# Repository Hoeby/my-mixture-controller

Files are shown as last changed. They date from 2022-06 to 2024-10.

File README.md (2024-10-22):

# mixture-controller
RC engine mixture controller.

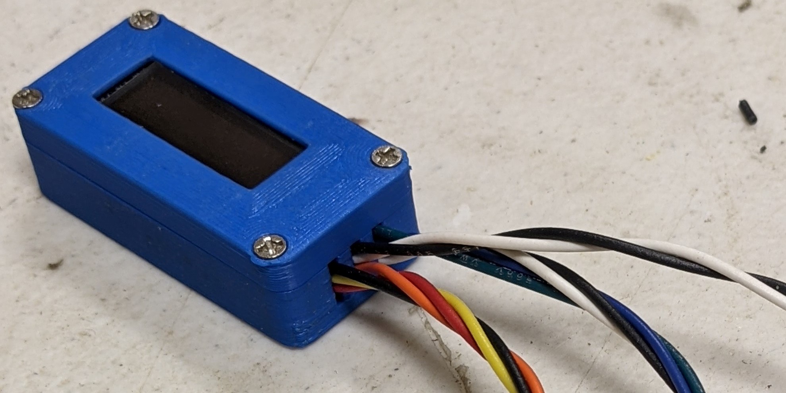
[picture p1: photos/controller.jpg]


This controller works with a stihl solenoid part number 0000 120 5111 and a custom solenoid housing (https://github.com/raleighcopter/my-mixture-controller/blob/main/photos/solenoid%20housing.pdf) to modulate gasoline flow to a conventional methanol carburator. This allows us to generate a custom fuel mixture curve on our transmitter that is slaved to the throttle channel output. The result is that we can vary the fuel:air mixture across the entire throttle range to make the engine run near stoichiometric fuel:air ratio at idle, full throttle, and every point in between. Without the solenoid and controller, our methanol engines run extremely rich in the middle. 

The controller takes an RC channel and maps a 1000 uS - 2000 uS channel pulse to a PWM solenoid pulse. Additionally, the controller measures atmospheric pressure and temperature and adjusts the fuel amount to maintain the ideal mixture regardless of the weather or altitude (which constantly changes as we fly our models). We have engines that were tuned at 85 degrees F that run just as well at 35 degrees F without touching the needles. 

I currently have my OS FT120-ii and Saito FA72 converted and Bert (the man behind the idea who designed the solenoid housing) has engines ranging from an asp 0.30 four stroke up to an ASP 1.6 boxer and a larger radial converted and running well. This conversion has been used on 2 stroke engines, 4 stroke engines, single  and twin cylinder engines and radial multi-cylinder engines.

I built the controller using a seeduino Xiao an IRLD110pbf MOSFET, a 2.2k resistor, a diode, a bmp280, and optionally, a 128x32 oled display and I've tested it on 4s NiMH and 2s LiFePo. Power comes in on the power and ground pads on the back of the Xiao. 

If you're powering your controller with a 2s LiFePo battery, wire a 1n4003 diode or something similar in the red wire before feeding power to the power pad or the Vcc pin. if you're powering your controller with a 4S NiMh, omit the diode and instead, wire a pololu s7v7f5 5 volt buck/boost converter inline.

The solenoid, bmp280, and optional display grab 3.3 volts from the Xiao's 3.3v pin. The MOSFET is wired to D3 and the RC channel is wired to D2. There's only 1 ground pad on the back and one ground pin so I doubled up on the pad on the back because I need 3 grounds.

I wired a 2.2k resistor across the MOSFET's gate and source (an 0805 smt resistor works really well here but a 1/8 watt resistor also works) and added a short piece of wire to those pins before I slipped some heat shrink over the separate pins. I soldered the wire that runs to the solenoid to the MOSFET's drain, trimmed the pins and then covered the entire MOSFET with heat shrink. After it was covered with heat shrink, I soldered the wire from the MOSFET's gate to D3 and the wire from the MOSFET's source to ground.

SDA and SCL from the bmp280 go to D4 and D5 and the optional display also uses these connections. if you measure resistance of about 10k between SDO and ground on the bmp280 it has a base address of 0x76. otherwise it has a base address of 0x77 and you need to change the base address at the top of the controller code. 

If you're building this with an oled display, wire the display to the same 4 points that the bmp280 is connected: 3.3v, ground, SDA, and SCL. You can wire it in parallel or in series with the bmp280.

if you're using this with an opentx transmitter and want s.port data, connect your s.port to pin 0 of the Xiao.

ebay/china is the least expensive source for bmp280 sensors at about $1 each and 128x32 oled displays at about $2.50. Be aware that we've seen fairly high failure rates on the China sourced bmp280 boards. As a result, the solenoid will signal a failed sensor at startup by buzzing for half a second and then remaining quiet for another half second and repeating indefinitely..

you'll need to install a few libraries in the arduino IDE: adafruit bmp280, adafruit ssd1306, adafruit GFX library and the frsky s.port sensor library by herman kruisman. you'll also need to add the seeeduino xiao board definition using the board manager.

build photos as well as parts lists and assembly instructions are on the wiki at https://github.com/raleighcopter/my-mixture-controller/wiki

for support, post in the thread at https://www.rcuniverse.com/forum/engine-conversions-92/11699946-electronic-solutions-modifying-glow-engines-all-sizes-gasoline.html

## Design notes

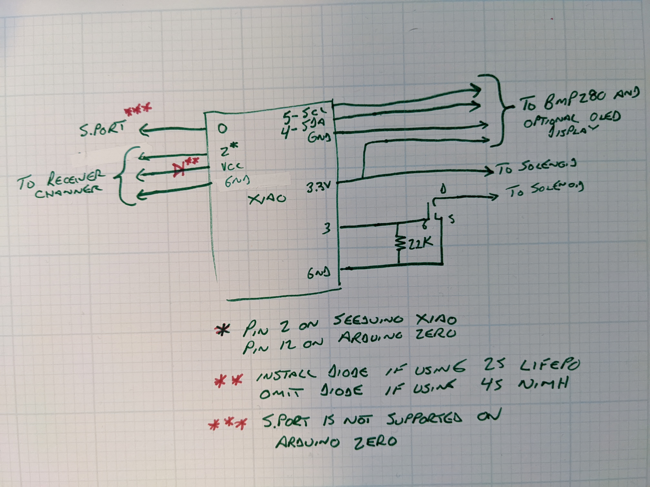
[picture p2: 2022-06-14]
photos/xiao schematic.jpg

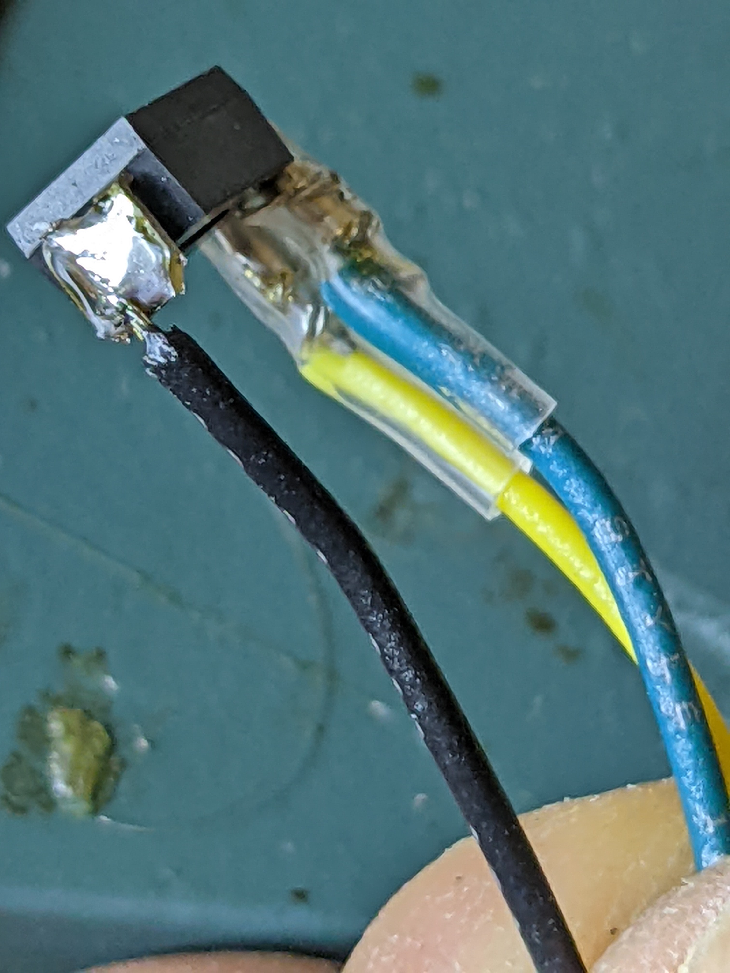
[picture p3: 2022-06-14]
photos/zero_11.jpg

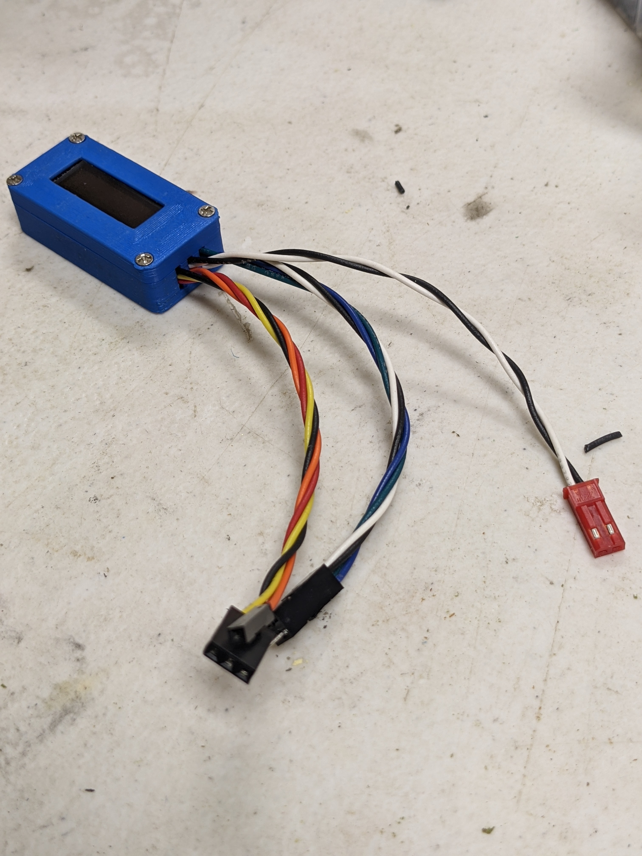
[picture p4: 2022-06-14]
photos/c1.jpg

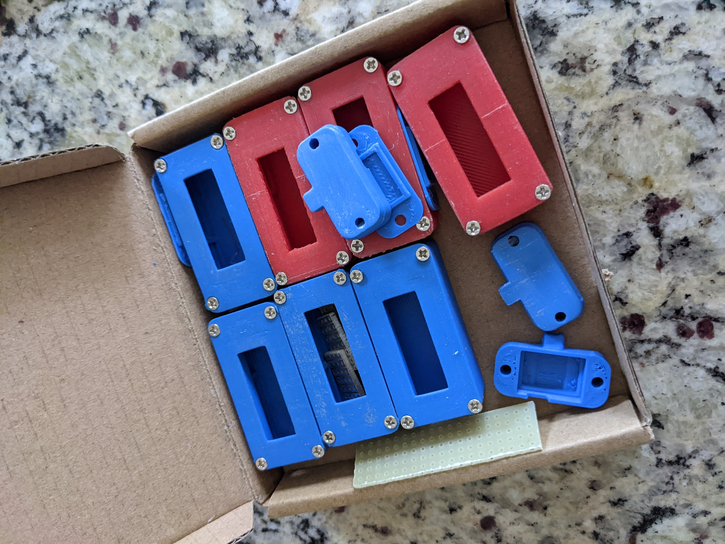
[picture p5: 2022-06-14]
photos/c2.jpg

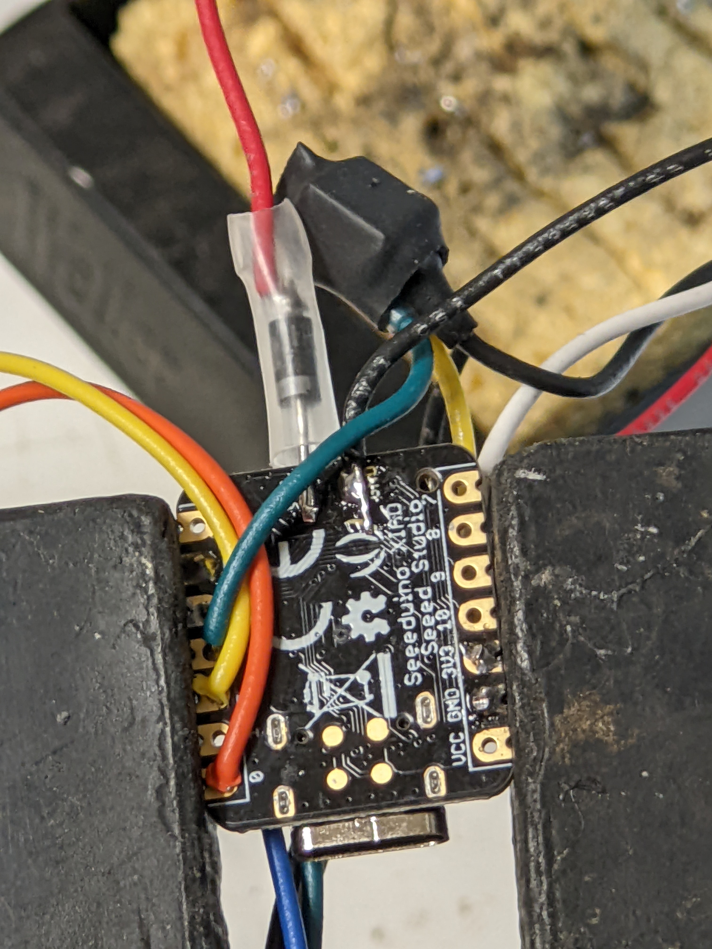
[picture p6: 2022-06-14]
photos/c12.jpg

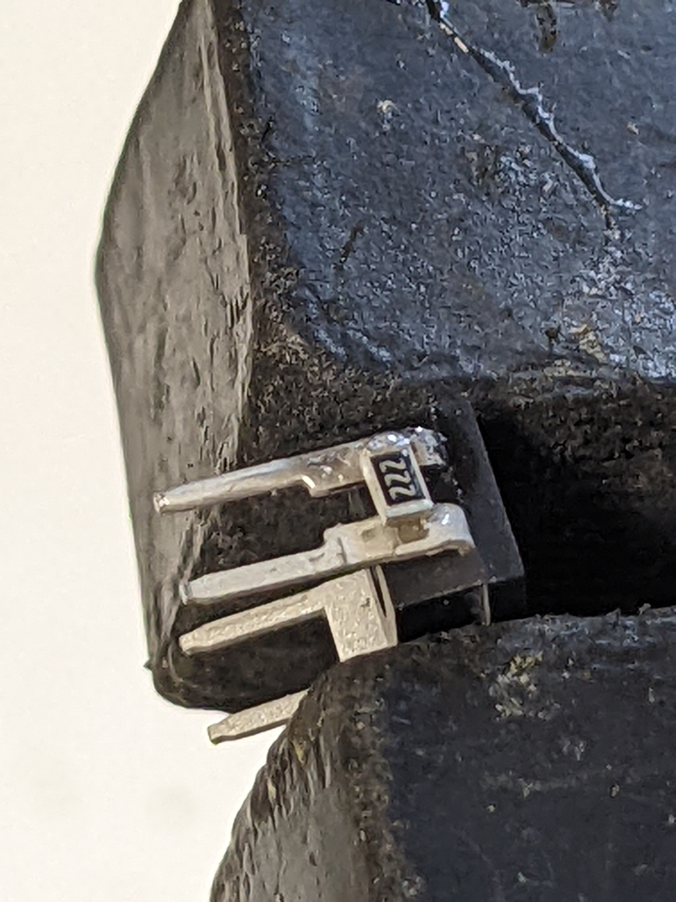
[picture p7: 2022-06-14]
photos/c4.jpg

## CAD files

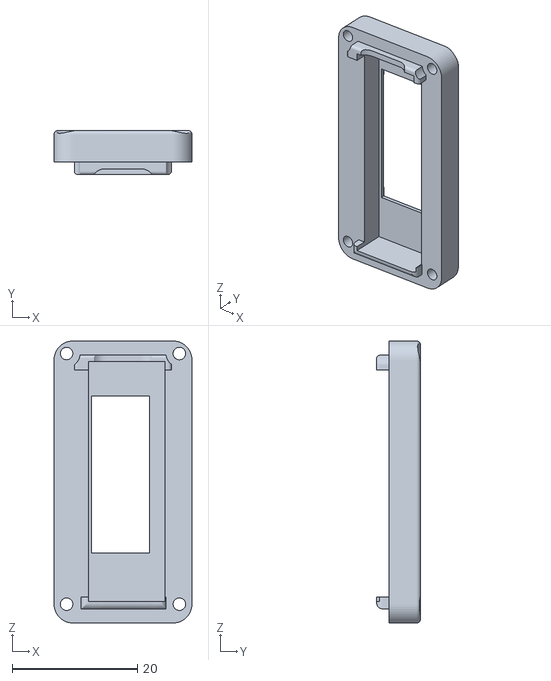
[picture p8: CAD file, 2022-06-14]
case_files/OLED lid.stl
22.0 x 7.00 x 45.0

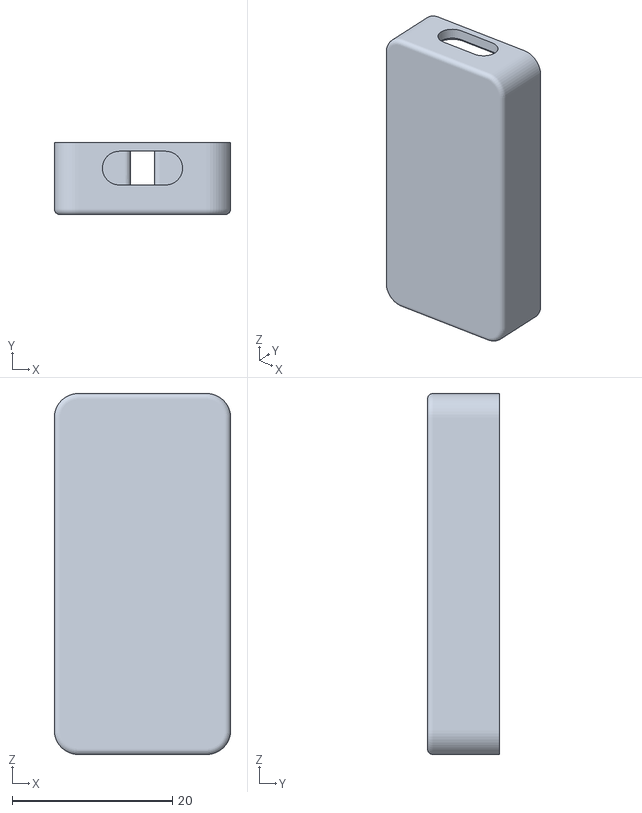
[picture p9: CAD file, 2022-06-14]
case_files/AMC case v9.stl
22.0 x 9.00 x 45.0

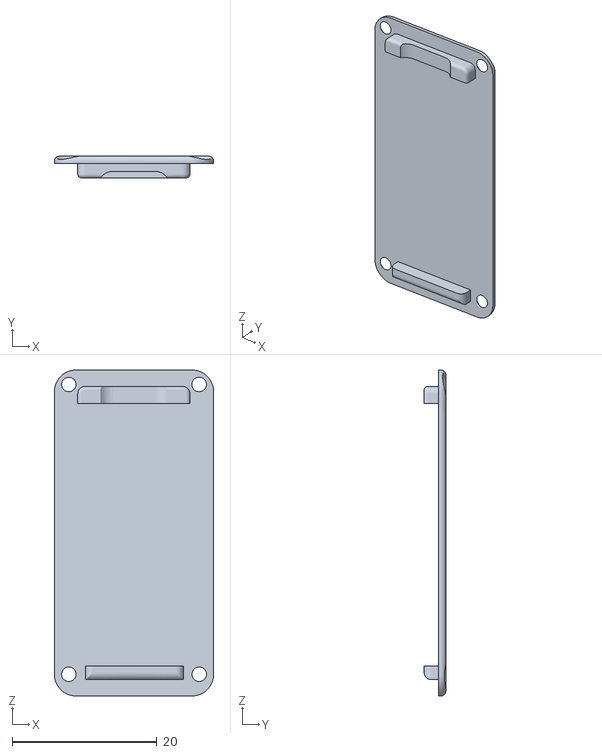
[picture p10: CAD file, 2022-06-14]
case_files/No OLED Lid.stl
22.0 x 3.00 x 45.0

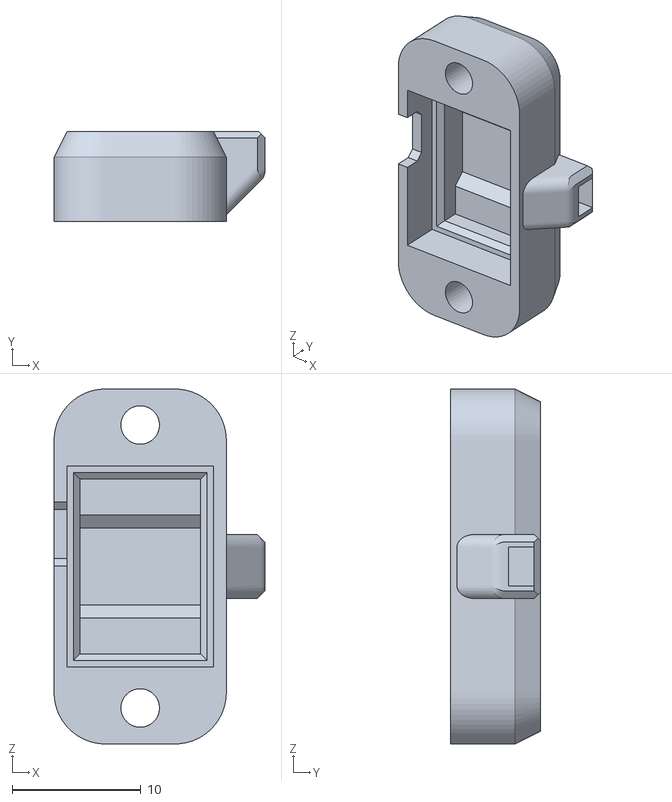
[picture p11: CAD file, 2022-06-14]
case_files/BMP280 Case.stl
16.4 x 7.00 x 27.6

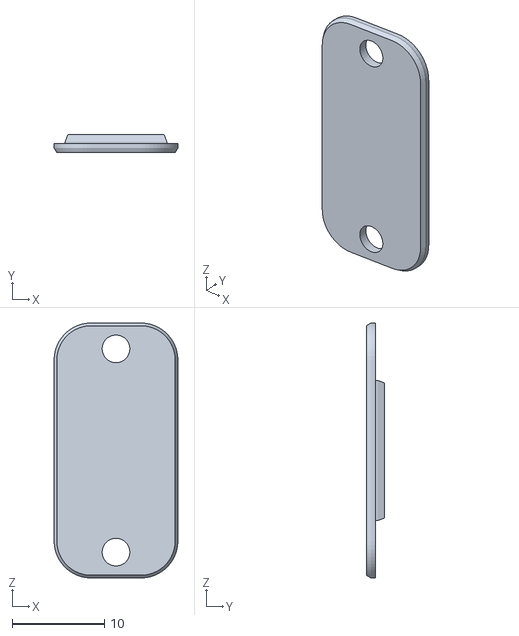
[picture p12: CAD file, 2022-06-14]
case_files/BMP280 cover.stl
13.4 x 2.00 x 27.6

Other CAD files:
brackets/asp ft1.6 bmp280 bracket v1.f3d
brackets/bmp280_bracket_OSft120.f3d
case_files/AMC case.f3d

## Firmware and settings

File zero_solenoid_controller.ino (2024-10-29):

//this code is written for the Arduino Zero by david taylor and released under the 
//GNU general public license V3.0. Permissions of this strong copyleft license are 
//conditioned on making available complete source code of licensed works and modifications,
//which include larger works using a licensed work, under the same license. Copyright and 
//license notices must be preserved. Contributors provide an express grant of patent rights.
// Also, Gary Cee from rcgroups is a douchebag 

//pin d3 controls the solenoid
//pin d12 is the rc channel input
//adjust reference temp (kelvin), pressure (paschal), and rc channel pin here
const int reference_temp = 283;
const int reference_pressure = 100000;

// Fallback temp and pressure replace actual measured values if the sensor fails during
// a flight. I estimate anything between this temp and 35 °F higher will cause the engine
// to run rich. Set fallback temp to the lowest temperature you're likely to fly in.
const int fallback_temp = 0;
const int fallback_pressure = 102000;
const int rc_functionPin = 12;

//OLED addresses are 0x3C or 0x3D
#define OLED_ADDR   0x3C

//BMP280 addresses are 0x76 or 0x77
#define BMP280_ADDR   0x76

//****************************************************************************************
// **********************  DO NOT EDIT ANYTHING BELOW THIS LINE  *************************
//****************************************************************************************

unsigned long old_time;
int update_display;
const long display_interval = 1000; 
volatile unsigned long pulse_start_time = 0L;
volatile unsigned long pulse_now = 0L;
volatile unsigned long channel_pulse = 0L;
volatile unsigned long pulse_old = 0L;
volatile unsigned long adjusted_pulse = 0L;
volatile unsigned long solenoid_pulse = 0L;
volatile unsigned long usable_pulse = 0L;
int channel;
int bmp_error = 0;
char _buffer[9];

#include <Wire.h>
#include <Adafruit_GFX.h>      // include Adafruit graphics library
#include <Adafruit_SSD1306.h>  // include Adafruit SSD1306 OLED display driver
#include <Adafruit_BMP280.h>   // include Adafruit BMP280 sensor library

Adafruit_BMP280 bmp; // I2C
Adafruit_SSD1306 display(-1);  // initialize Adafruit display library, share reset with xiao reset

void setup() {
  
// initialize the SSD1306 OLED display with I2C address = 0x3C
  display.begin(SSD1306_SWITCHCAPVCC, OLED_ADDR);
// clear the display buffer.
  display.clearDisplay();
  display.setTextSize(1);   // text size = 1
  display.setTextColor(WHITE, BLACK);  // set text color to white and black background

//uncomment the next line to debug  
//SerialUSB.begin(115200);

  pinMode(rc_functionPin, INPUT);
  attachInterrupt(rc_functionPin, RCpinread, CHANGE);

  if (!bmp.begin(BMP280_ADDR, BMP280_CHIPID)) {
//  SerialUSB.println(F("Could not find a valid BMP280 sensor, check wiring or try a different address!"));
    bmp_error = 1;
  }
  
  bmp.setSampling(Adafruit_BMP280::MODE_NORMAL,     /* Operating Mode. */
                  Adafruit_BMP280::SAMPLING_X2,     /* Temp. oversampling */
                  Adafruit_BMP280::SAMPLING_X16,    /* Pressure oversampling */
                  Adafruit_BMP280::FILTER_X16,      /* Filtering. */
                  Adafruit_BMP280::STANDBY_MS_500); /* Standby time. */

//check for bad data from bmp280 and set error flag
  if (bmp.readTemperature() >= 85) bmp_error = 1;
  if (bmp.readPressure() >= 110000) bmp_error = 1;                  

//setup timer regisiters
  pinMode(3, OUTPUT);
  REG_GCLK_GENDIV = GCLK_GENDIV_DIV(232) |       // Divide the main clock down by some factor to get generic clock
                    GCLK_GENDIV_ID(4);            // Select Generic Clock (GCLK) 4
  while (GCLK->STATUS.bit.SYNCBUSY);              // Wait for synchronization

  REG_GCLK_GENCTRL = GCLK_GENCTRL_IDC |           
                     GCLK_GENCTRL_GENEN |         // Enable GCLK4
                     GCLK_GENCTRL_SRC_DFLL48M |   // Set the 48MHz clock source
                     GCLK_GENCTRL_ID(4);          // Select GCLK4
  while (GCLK->STATUS.bit.SYNCBUSY);              // Wait for synchronization

// Enable the port multiplexer for the digital pin. 
  PORT->Group[g_APinDescription[3].ulPort].PINCFG[g_APinDescription[3].ulPin].bit.PMUXEN = 1;
  
//Connect the TCC0 timer to digital output - port pins are paired odd PMUO and even PMUXE 
  PORT->Group[g_APinDescription[4].ulPort].PMUX[g_APinDescription[4].ulPin >> 1].reg = PORT_PMUX_PMUXO_F | PORT_PMUX_PMUXE_F;

// Feed GCLK4 to TCC0 and TCC1
  REG_GCLK_CLKCTRL = GCLK_CLKCTRL_CLKEN |         // Enable GCLK4 to TCC0 and TCC1
                     GCLK_CLKCTRL_GEN_GCLK4 |     // Select GCLK4
                     GCLK_CLKCTRL_ID_TCC0_TCC1;   // Feed GCLK4 to TCC0 and TCC1
  while (GCLK->STATUS.bit.SYNCBUSY);              // Wait for synchronization

//Set for Single slope PWM operation: timers or counters count up to TOP value and then repeat
  REG_TCC1_WAVE |= TCC_WAVE_WAVEGEN_NPWM;        // Reverse the output polarity on all TCC0 outputs
  while (TCC1->SYNCBUSY.bit.WAVE);               // Wait for synchronization
 
  REG_TCC1_PER = 6144;                           // This sets the rate or frequency of PWM signal 
  while (TCC1->SYNCBUSY.bit.PER);                // Wait for synchronization
  
// Set the PWM signal to output 50% duty cycle initially 
  REG_TCC1_CC1 = 3072;                           // this sets the pwm duty cycle. values from 0 6145 are valid. 
  while (TCC1->SYNCBUSY.bit.CC1);                // Wait for synchronization

// Set prescaler and enable the outputs
  REG_TCC1_CTRLA |= TCC_CTRLA_PRESCALER_DIV1 |    // Divide GCLK4 by 1
                    TCC_CTRLA_ENABLE;             // Enable the TCC0 output
  while (TCC1->SYNCBUSY.bit.ENABLE);              // Wait for synchronization

}

//############################################################################

void loop() {

while(bmp_error == 1) {
  display.clearDisplay();
  display.setCursor(0, 0);
  display.setTextSize(2);
  display.println("  SENSOR");
  display.println("  ERROR");
  display.display();
  REG_TCC1_CC1 = 3072;
  delay(500);
  REG_TCC1_CC1 = 0;
  delay(500);  
}

// get temperature and pressure from library
  float temp     = bmp.readTemperature();   // get temperature
  float pressure = bmp.readPressure();      // get pressure
  if (temp >= 85) temp = fallback_temp;
  if (pressure >= 110000) pressure = fallback_pressure;  
  
//adjust for temp and pressure  
    adjusted_pulse = (usable_pulse * ((reference_temp/(temp + 273))*(pressure/reference_pressure))) * 6.145;
    solenoid_pulse = constrain(adjusted_pulse, 0, 6145);
    solenoid_pulse = map(solenoid_pulse, 0, 6145, 6145, 0);

//adjust for temp and pressure  
      
    adjusted_pulse = (usable_pulse * ((reference_temp/(temp + 273))*(pressure/reference_pressure))) * 6.145; 
    solenoid_pulse = constrain(adjusted_pulse, 0, 6145);
    solenoid_pulse = map(solenoid_pulse, 0, 6145, 6145, 0);
      
// load pulse value into timer register
    REG_TCC1_CC1 = (solenoid_pulse); 
    while (TCC1->SYNCBUSY.bit.CC1);

/*/  uncomment this section to debug  
    SerialUSB.print(bmp.readTemperature());
    SerialUSB.print(" *C     ");
    SerialUSB.print(bmp.readPressure());
    SerialUSB.print(" Pa     ");
    SerialUSB.print(adjusted_pulse);
    SerialUSB.print("  ");     
    SerialUSB.print(solenoid_pulse);
    SerialUSB.print("  ");
    SerialUSB.println(channel_pulse);
*/

// do this once every display_interval.
  unsigned long current_time = millis();
  if(current_time - old_time >= display_interval){
        
// print data on the LCD

//clear the display
  display.clearDisplay();
  
// print temperature
  if(temp < 0)
    sprintf(_buffer, "-%02u.%01u C", (int)abs(temp), (int)(abs(temp) * 100) % 10 );
  else
    sprintf(_buffer, "%02u.%01u C", (int)temp, (int)(temp * 100) % 10 );
  display.setCursor(0, 0);
  display.setTextSize(1);
  display.print(_buffer);
 
// print degree symbol ( ° )
 if(temp < 0)
   display.drawCircle(32, 1, 1, WHITE);
 else
   display.drawCircle(26, 1, 1, WHITE);
   
// print pressure
  if(pressure < 100000)
    sprintf(_buffer, "%03u.%01u mB", (int)(pressure/100), (int)((uint32_t)pressure % 10));
  else
    sprintf(_buffer, "%04u.%01umB", (int)(pressure/100), (int)((uint32_t)pressure % 10));
  display.setCursor(0,8);
  display.setTextSize(1);
  display.print(_buffer);


//print correction
  
  float corr =  1000 * (reference_temp/(temp+273)*(pressure/reference_pressure)); 
  if(corr>=1000){
    sprintf(_buffer, "%03u.%01u", (int)(corr/10), (int)((uint32_t)corr % 10));
    display.setCursor(60,0);
    }
  else {
    sprintf(_buffer, "%02u.%01u", (int)(corr/10), (int)((uint32_t)corr % 10));
    display.setCursor(70,0);
    }
  display.setTextSize(2);
  display.print(_buffer);

// print a % symbol
  display.drawCircle(120, 1, 1, WHITE);
  display.drawCircle(123, 8, 1, WHITE);
  display.drawLine(123,1,120,8,WHITE);

//print channel pulse
  sprintf(_buffer, "%04u Channel Pulse", (int)(channel));
  display.setCursor(0,16);
  display.setTextSize(1);
  display.print(_buffer);  


// print solenoid pulse
  sprintf(_buffer, "%04u Solenoid Pulse", (int)(solenoid_pulse));
  display.setCursor(0,24);
  display.setTextSize(1);
  display.print(_buffer);  

// update the display
  display.display();

//reset the timer flag and set a new one
  old_time = millis();
  update_display=0;
}
}


// this function reads the rc channel pulse time
void RCpinread() {
  pulse_now = micros();
  pulse_old = channel_pulse;
  channel_pulse = pulse_now - pulse_start_time;
  pulse_start_time = pulse_now;
  if(channel_pulse < 988) {
    channel_pulse = pulse_old; //throw out low values
  }else if(channel_pulse > 2012) {
    channel_pulse = pulse_old; //throw out high values
  }
  channel_pulse = constrain (channel_pulse, 1000, 2000);
  channel = channel_pulse;
  usable_pulse = channel_pulse - 1000;
}

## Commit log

2023-09-19 fixed solenoid action, fixed channel pulse display on oled
2023-09-19 Add files via upload
    bolder flight systems PWM library by brian taylor
2023-09-20 Update xiao_sbus_controller
    added the ability to switch 3 digital pins based on rc channel inputs. channels and pins can be configured at the top of the source
2023-09-24 added telemetry devices and thermistors.
    still to do: read RPM and control the Aux1 channel used for the air pump
2024-02-03 added bmp280 bracket
    [bmp280_bracket_ft160.f3d]
2024-10-29 Update xiao_solenoid_controller.ino
    fixed clock divider
    [xiao_solenoid_controller.ino]
2024-10-29 Update zero_solenoid_controller.ino
    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
    [zero_solenoid_controller.ino]
